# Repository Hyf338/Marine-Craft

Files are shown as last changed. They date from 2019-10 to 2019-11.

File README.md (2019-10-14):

# JMU_ETA_Fly on The Sea

<p align="center">
  
</p>

## 简介
2019集大电协 海洋航行器

工具     | 描述
-------- | -----
Altium Design|PCB设计
Keil|软件编程
123D Design|3D软件

## 目录说明
````
+——Marine craft
|---- Dos: 【设计文档】
|---- 3D model: 【3D模型】
|----+ hardware:【电路设计】  
|       ├──Control V1.0【主控板】
|       ├──Control V2.0【主控电路板-最终版】
|       ├──Infrared reception【红外接收盘】
|       ├──Power Transfer【临时电源转接】
|---+ software:【软件设计】
|       ├──Craft【航行器程序】
|       ├──remoted【遥控器调试】
````

## 3D model
- 红外屏蔽罩3D模型设计

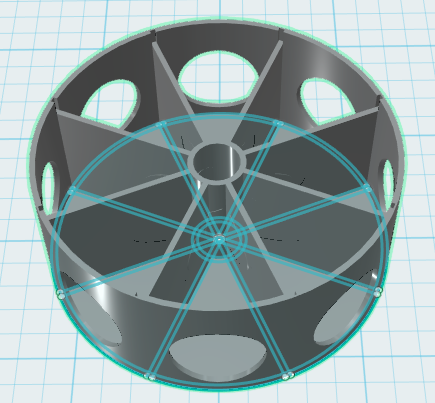
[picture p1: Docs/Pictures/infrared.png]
3D信号屏蔽罩 信号屏蔽罩


## Hardware
- 主控与外设描述

硬件     | 描述
-------- | -----
芯片信号  |STM32F103
串口  | ZIGBEE
蓝牙  | HC-05
舵机  | EMAX ES08MA
电机|380
显示|oled

- 端口定义

功能     | 端口
-------- | -----
红外盘接收  |A8.B13.B14.B15.C6.C7.C8.C9
蓝牙&串口  | USART2_TX -- A2  . USART2_RX -- A3
蓝牙&串口  | USART1_TX -- A9  . USART1_RX -- A10
舵机  | TIM2_CH2 -- A1
电机|TIM3_CH1 --B4 .   TIM3_CH2 -- B5
OLED|DC -- B6. RES -- B7 . D1 -- B8 . D0 -- B9

- [x]  船舶主控板

- 航行器主控板模块流程图

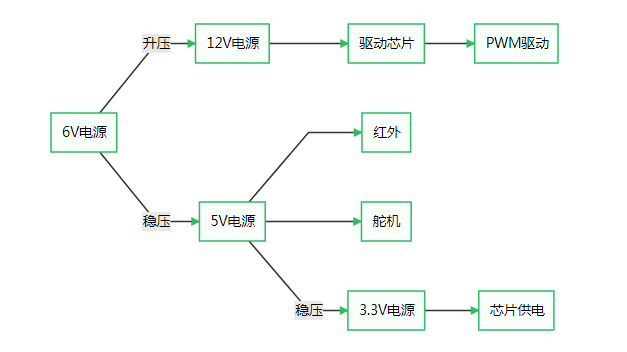
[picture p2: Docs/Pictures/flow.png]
流程图


- 航行器主控板

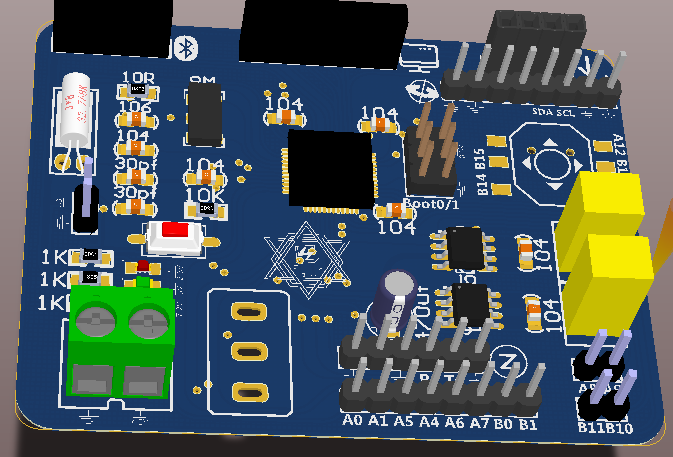
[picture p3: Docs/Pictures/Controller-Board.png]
主控板


- [x] 一体化红外接收盘

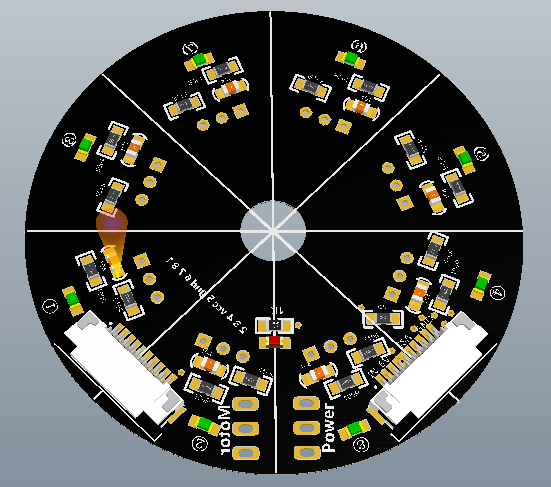
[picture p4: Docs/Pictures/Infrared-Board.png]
一体化红外接收盘


## Software

### 两种模式

- [x] 自动追踪模式
- [x] 遥控模式
- 数据包通信协议

| 编号 | 1 | 2 | 3 | 4 | 5 | 6 | 7 | 
| --- | --- | --- | --- | --- | --- | --- | --- |
| 数据所代表的含义 | 模式位 | 包头 | 包头 | 数据长度位 | 舵机 | 电机 | 校验 | 
| 说明 | 1-遥控、0-追踪 | AA | 55 | 2 | Servo | Motor | 累加 |
| 数组编号 | 0 | 1 | 2 | 3 | 4 | 5 | 6 |

## 作品

### 船模

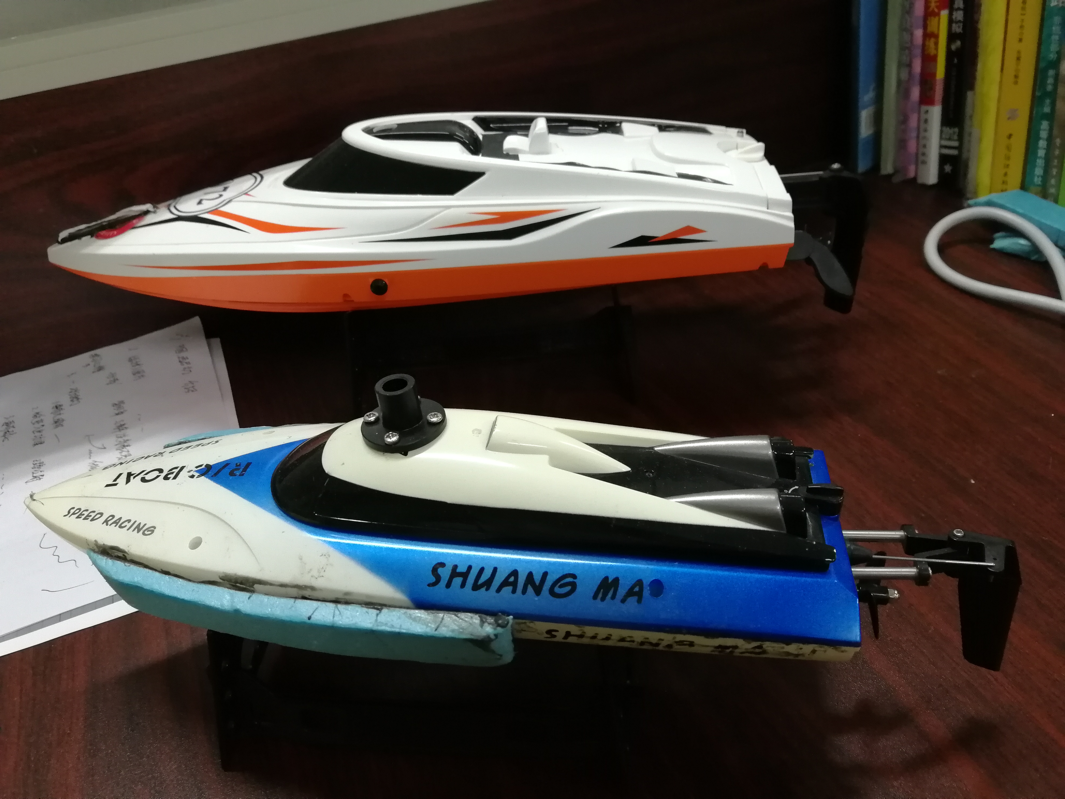
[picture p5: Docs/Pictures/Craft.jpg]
航行器


### 遥控器

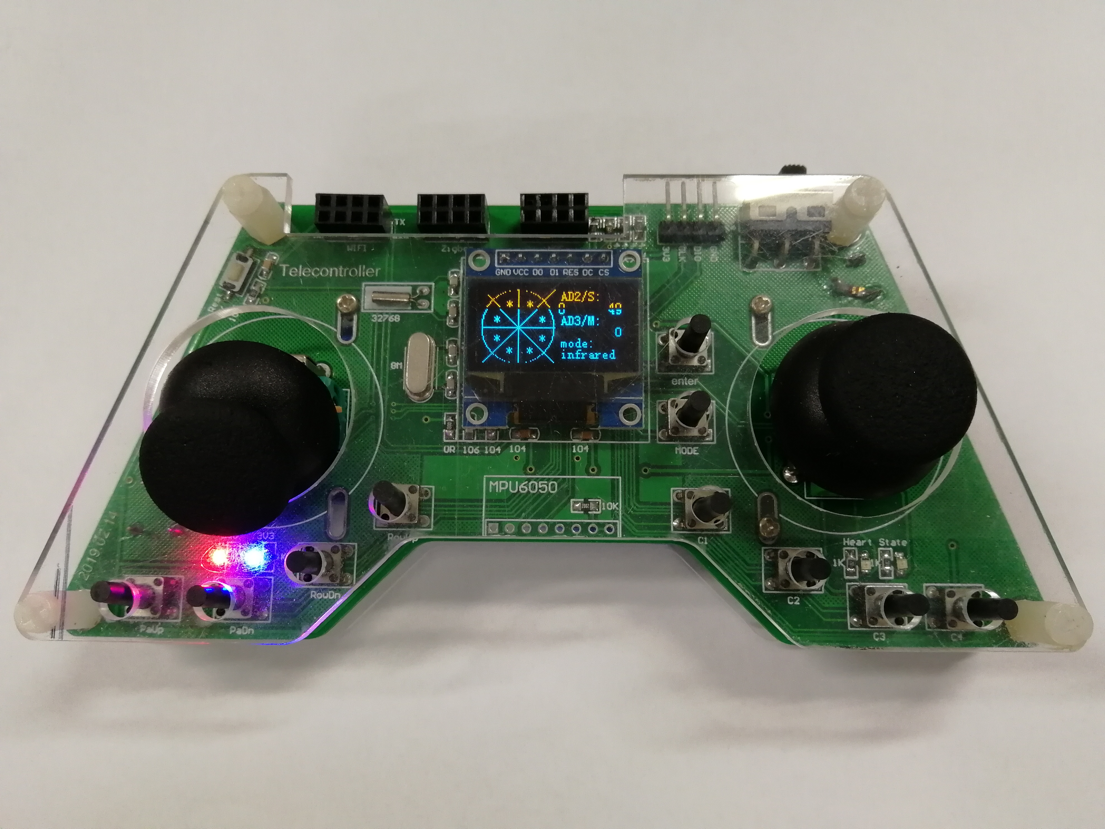
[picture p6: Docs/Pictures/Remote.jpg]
遥控器


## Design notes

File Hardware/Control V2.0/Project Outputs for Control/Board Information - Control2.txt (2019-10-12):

Board Information Report
Filename     : D:\AD\船模主控板\Control\Control2.PcbDoc
Date         : 2019/3/17
Time         : 16:33:21
Time Elapsed : 00:00:00

Routing Information
    Routing completion, 100.00%
    Connections, 214
    Connections routed, 214
    Connections remaining, 0
count : 4

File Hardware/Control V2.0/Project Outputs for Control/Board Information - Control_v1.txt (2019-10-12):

Board Information Report
Filename     : C:\Users\dell\Desktop\JMU_ETA_Fly-on-The-Sea\船模主控板\Control\Control_v1.1.PcbDoc
Date         : 2019/6/20
Time         : 21:29:51
Time Elapsed : 00:00:00

Routing Information
    Routing completion, 100.00%
    Connections, 204
    Connections routed, 204
    Connections remaining, 0
count : 4

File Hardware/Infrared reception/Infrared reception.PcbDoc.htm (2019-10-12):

Reporting Options

# File in Previous Format

Date | : | 2019/10/12
Time | : | 8:33:09
Filename | : | D:\Git Project\Marine Craft\Infrared reception\PCB_Project\Infrared reception.PcbDoc

Version | Warning

This file was generated by an earlier version of the software

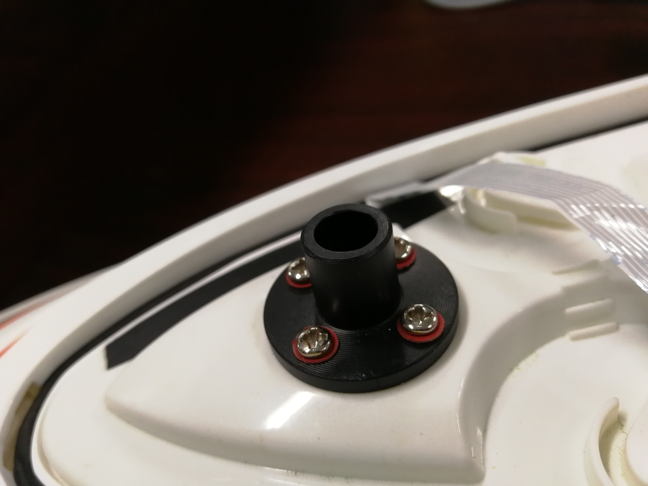
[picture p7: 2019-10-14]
Docs/Pictures/Support.jpg

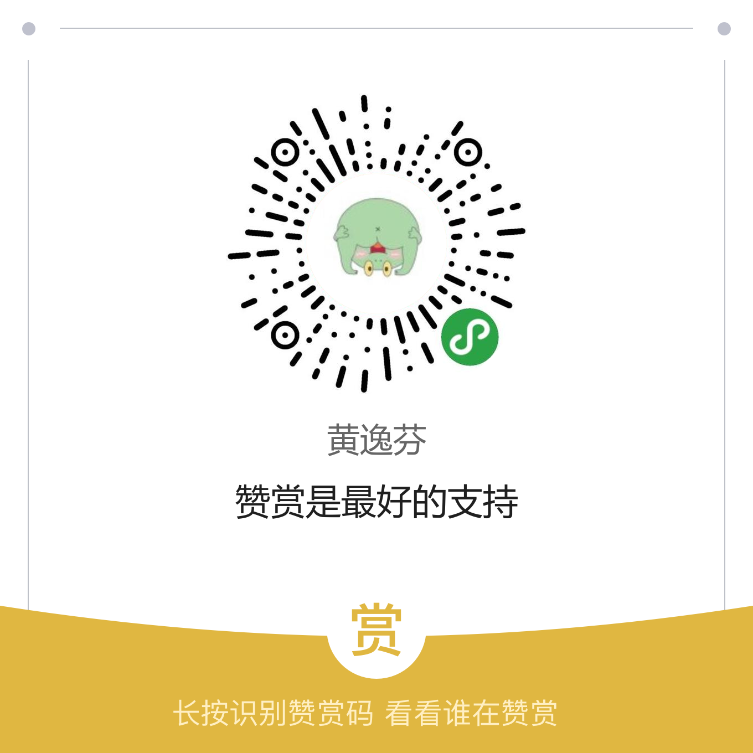
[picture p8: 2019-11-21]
Docs/Pictures/zan.png

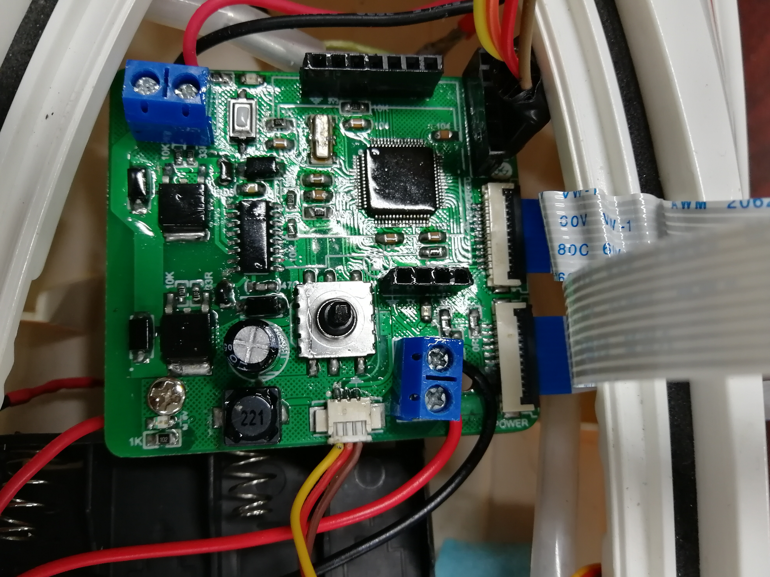
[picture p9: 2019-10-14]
Docs/Pictures/Board.jpg

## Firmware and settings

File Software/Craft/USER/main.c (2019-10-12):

#include "stm32f10x.h"
#include "delay.h"
#include "sys.h"
#include "timer.h"
#include "key.h"
#include "oled.h"
#include "control.h"
#include "usart.h"



int Motor1=150;
int Motor2=0;
u8 key_v=0,mode=0;
u8 receive_motor=0,receive_servo=0;
int servo=1210;
extern int Expect_servo;
extern int servo_PWM;
extern u8 infrared;
extern void infrared_Init(void);
extern u8 infrared_bit_move(void);
extern void infrared_receive(void);
extern void TIM4_Int_Init(u16 arr,u16 psc);
extern void servo_PD(void);
extern void infrared_receive_1(void);
extern void infrared_receive_2(void);


void page()
{
			static u8 x=0,y=0;
	draw_circle(35,30,30);
		for(x = 70;x>=30;x--)
		{
				OLED_DrawPoint(108-0.5*x,x,1);//画斜线 斜率≈√3/3
				OLED_DrawPoint(17 +0.5*x,x,1);
				y = 30-x;
				OLED_DrawPoint(64-0.5*y,y,1);
				OLED_DrawPoint(64+0.5*y,y,1);
			  OLED_Refresh_Gram();//更新显示到OLED
		}

	OLED_Refresh_Gram();
}


 int main(void)
 {	
  KEY_Init(); //IO初始化
	delay_init();	    	 //延时函数初始化	 
	OLED_Init();//OLED初始化
  uart2_init(115200);
//  Boot_Animation();	
	NVIC_PriorityGroupConfig(NVIC_PriorityGroup_2); 	 //设置NVIC中断分组2:2位抢占优先级，2位响应优先级
 	TIM3_PWM_Init(499,71);	 //72分频，500重装载值  f=2k Hz   电机
	TIM2_PWM_Init(20000 ,71); //72分频，20000重装载值   f= 50 Hz； 舵机
	TIM4_Int_Init(50000,35);//144分频，50000重装载值   f= 10Hz，T=100ms；红外接收检测周期为108ms；采集时间
	TIM_ITConfig(TIM4,TIM_IT_Update,DISABLE ); //关闭定时器TIM4中断，
	
	
//	OLED_ShowString(10, 5,(u8 *)"2019.3.17",12);
//	OLED_ShowString(10,15,(u8 *)"Motor1:",12);
//	OLED_ShowString(10,25,(u8 *)"Servo:",12);
//	OLED_ShowString(10,35,(u8 *)"infrared:",12);
//	OLED_ShowString(10,45,(u8 *)"servo_PWM:",12);
//	OLED_Refresh_Gram();
	infrared_Init();
	TIM_SetCompare2(TIM2,1210);	//舵机
	delay_ms(10);
	 
  while(1)
	{
 	
		
		key_v=KEY_Scan(0);
	
		if(key_v==KEY_UP_PRES) Motor1+=10;
		if(key_v==KEY_DOWM_PRES) Motor1-=10;
		
//		OLED_ShowNum(75,15,Motor1,3,12);
//		OLED_ShowNum(85,35,infrared,3,12);
//		OLED_ShowNum(85,45,servo,4,12);
		if(mode==0)
		{
			Motor1=150;
			TIM_ITConfig(TIM4,TIM_IT_Update,ENABLE ); //使能指定的TIM3中断,允许更新中断
//			infrared_receive_1();
			infrared_receive_1();
			TIM_ITConfig(TIM4,TIM_IT_Update,DISABLE ); //关闭定时器TIM4中断，
			servo=Expect_servo;
			if(infrared==0xff)  Motor1=0; 
				else Motor1=150;
		}
		if(mode==1)
		{
			Motor1=2*receive_motor;
			servo=1210+5*(50-receive_servo);
		}
		
	 servo= (servo>1600)? 1600:servo;
	 servo= (servo<850)? 850:servo;
				
		
		TIM_SetCompare2(TIM2,servo);	//舵机
		TIM_SetCompare2(TIM3,Motor2);		   
		TIM_SetCompare1(TIM3,Motor1);	 
		page();
	}	 	
 }

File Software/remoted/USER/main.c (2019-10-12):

#include "stm32f10x.h"

#include "mpuiic.h"
#include "mpu6050.h"
#include "inv_mpu.h"
#include "inv_mpu_dmp_motion_driver.h" 

#include "delay.h"
#include "oled.h"
#include "usart.h"
#include "timer.h"
#include "control.h"
#include "key.h"
#include "adc.h"
#include "display.h"

/****************************************************************
硬件连接:

Zigbee(uart1):			ESP8266(uart2):				NRF24L01:
TX -> PA9						TX -> PA2							NRF_CE -> PA0
RX -> PA10					RX -> PA3							NRF_CS -> PA1
																					NRF_IRQ -> PA4
																					SPI1_CLK -> PA5
																					SPI1_MISO -> PA6
																					SPI1_MOSI -> PA7
												
指示灯:							蜂鸣器:								OLED:
State -> PB12				BUZZ -> PB4						D0 -> PB9
Heart -> PB13															D1 -> PB8
																					RES -> PB7
																					DC -> PB6
																					
按键:								摇杆:										
PaUp -> PC4         Throttle -> PC2					
PaDn -> PC5         Yaw -> PC3							
RowUp -> PB1        Pitch -> PC1
RowDn -> PB0        Roll -> PC0
enter -> PC9
MODE -> PC8
C1 -> PB14
C2 -> PB15
C3 -> PC6
C4 -> PC7


MPU6050:
IMUSCL -> PB10
IMUSDA -> PB11
****************************************************************/

float pitch,roll,yaw; 		//欧拉角									//俯仰角		翻滚角		横向角
short aacx,aacy,aacz;		//加速度传感器原始数据
short gyrox,gyroy,gyroz;	//陀螺仪原始数据
short temp;					//温度
char AD1=0,AD2=0,AD3=0,AD4=0;
short AD1_get=0,AD2_get=0,AD3_get=0,AD4_get=0;

extern signed short int Pitch,Roll,Yaw;
extern u8 send_data;

typedef enum
{
	sunday,  //0
	monday,
	thuesday,
	wednesday = 5,
	tuesday,
	friday,
	saturday
}WeekType;

WeekType week;

 int main(void)
 {
	 
	 delay_init();	    	//延时函数初始化
	 NVIC_PriorityGroupConfig(NVIC_PriorityGroup_2);// 设置中断优先级分组2
	
	
	 OLED_Init();
	 BUZZ_Init();
//	 uart_init(115200);//zigbee串口通信
	 KEY_Init(); //IO初始化
	 Adc_Init();

	 
	 MPU_Init();					//初始化MPU6050
	 
	 while(mpu_dmp_init())
   {
		OLED_ShowString1(0,3,"Error");
		delay_ms(200);
   }
	 
   TIM4_Int_Init(50000,107);
	 TIM_Cmd(TIM4, ENABLE);  //使能TIMx
		OLED_Clear();
   while(1)
	 {		 
		 AD1_get=Get_Adc_Average(ADC_Channel_10,10);
		 AD2_get=Get_Adc_Average(ADC_Channel_11,10);
		 AD3_get=Get_Adc_Average(ADC_Channel_12,10);
		 AD4_get=Get_Adc_Average(ADC_Channel_13,10);
		 
		 AD2=100*AD2_get/4096;
		 AD3=100*(4096-AD3_get)/4096;
		 
		 Page2();
	 }
 }

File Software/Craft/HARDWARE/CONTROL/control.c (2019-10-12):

#include "sys.h"
#include "stm32f10x.h"
#include "control.h"
#include "timer.h"
#include "delay.h"

#define servo_mid 1210
#define N 5

int Expect_servo=0;
int servo_PWM=1210;
int servo_last=0;
int Servo_err=0;
//---------------------------
u8 infrared=0x00;//初始状态
char temp=0x00;
char infrared_flag=0;
u8  infrared_bit[8]={0};
int servo_err[4]={0,0,0,0};
u8 sum=0;
int infrared_err=0;

/*红外引脚初始化函数*/
void infrared_Init(void) //IO初始化
{ 
 	GPIO_InitTypeDef GPIO_InitStructure;
 
 	RCC_APB2PeriphClockCmd(RCC_APB2Periph_GPIOA|RCC_APB2Periph_GPIOB|RCC_APB2Periph_GPIOC,ENABLE);//使能PORTA,PORTE时钟

	GPIO_InitStructure.GPIO_Pin  = GPIO_Pin_6 |GPIO_Pin_7|GPIO_Pin_8|GPIO_Pin_9;//
	GPIO_InitStructure.GPIO_Mode = GPIO_Mode_IPU; //设置成上拉输入
 	GPIO_Init(GPIOC, &GPIO_InitStructure);//初始化GPIOC
	
	GPIO_InitStructure.GPIO_Pin  = GPIO_Pin_8;//
	GPIO_InitStructure.GPIO_Mode = GPIO_Mode_IPU; //设置成上拉输入
 	GPIO_Init(GPIOA, &GPIO_InitStructure);//初始化GPIOA
	
	GPIO_InitStructure.GPIO_Pin  = GPIO_Pin_13|GPIO_Pin_14|GPIO_Pin_15;//
	GPIO_InitStructure.GPIO_Mode = GPIO_Mode_IPU; //设置成上拉输入
 	GPIO_Init(GPIOB, &GPIO_InitStructure);//初始化GPIOA
}


/*红外检测位移函数，
	目标：把八个红外头按位移入一个char型数据，方便写switch和case语句
	数值说明：0为接收到红外信号，1未接收到信号。无信号的状态为0xff
*/
	
u8 infrared_bit_move(void)
{
	
	char i=0;
	infrared=0xff;
	temp=0x00;
	
	while(!infrared_flag)
	{
		infrared_bit[0]=GPIO_ReadInputDataBit(GPIOB,GPIO_Pin_13);//1-8号红外按序排列
		infrared_bit[1]=GPIO_ReadInputDataBit(GPIOA,GPIO_Pin_8);
		infrared_bit[2]=GPIO_ReadInputDataBit(GPIOC,GPIO_Pin_9);
		infrared_bit[3]=GPIO_ReadInputDataBit(GPIOC,GPIO_Pin_8);
		infrared_bit[4]=GPIO_ReadInputDataBit(GPIOC,GPIO_Pin_7);
		infrared_bit[5]=GPIO_ReadInputDataBit(GPIOC,GPIO_Pin_6);
		infrared_bit[6]=GPIO_ReadInputDataBit(GPIOB,GPIO_Pin_15);
		infrared_bit[7]=GPIO_ReadInputDataBit(GPIOB,GPIO_Pin_14); 
	
		for(i=0;i<8;i++)//检测到为0，bit[0] 最低位
		{
			temp = temp<<1;
			temp|=infrared_bit[7-i];
		}
		infrared&=temp;
		
	}
	
	if(infrared_flag==1) infrared_flag=0;
	
	return infrared;
}




/*红外接收处理函数*/
void infrared_receive_1()
{
	infrared=filter();
	switch(infrared)
		
	{
		case 0xfe:Expect_servo=900;break;//1号
		case 0xfd:Expect_servo=900;break;//2
		case 0xfb:Expect_servo=1600;break;//3
		case 0xf7:Expect_servo=1600;break;//4
		case 0xef:Expect_servo=1600;break;//5
		case 0xdf:Expect_servo=1600;break;//6
		case 0xbf:Expect_servo=900;break;//7
		case 0x7f:Expect_servo=1210;break;//8
		
		case 0x7e:Expect_servo=900;break;
		case 0xfc:Expect_servo=900;break;
		case 0xf9:Expect_servo=900;break;
		case 0xf3:Expect_servo=1600;break;
		case 0xe7:Expect_servo=1600;break;
		case 0xcf:Expect_servo=1600;break;
		case 0x9f:Expect_servo=1210;break;
		case 0x3f:Expect_servo=900;break;
		
		case 0x3e:Expect_servo=1200;break;
		case 0x7c:Expect_servo=900;break;
		case 0xf8:Expect_servo=900;break;
		case 0xf1:Expect_servo=1600;break;
		case 0xe3:Expect_servo=1600;break;
		case 0xc7:Expect_servo=1600;break;
		case 0x8f:Expect_servo=900;break;
		case 0x1f:Expect_servo=900;break;
		
		case 0x1e:Expect_servo=900;break;
		case 0x3c:Expect_servo=900;break;
		case 0x78:Expect_servo=900;break;
		case 0xf0:Expect_servo=1600;break;
		case 0xe1:Expect_servo=1600;break;
		case 0xc3:Expect_servo=1600;break;
		case 0x87:Expect_servo=1600;break;
		case 0x0f:Expect_servo=1210;break;
		
		case 0xce:Expect_servo=1600;break;
		case 0x1c:Expect_servo=1600;break;
		case 0x38:Expect_servo=1600;break;
		case 0x70:Expect_servo=1600;break;
		case 0xe0:Expect_servo=900;break;
		case 0xc1:Expect_servo=1200;break;
		case 0x83:Expect_servo=900;break;
		case 0x07:Expect_servo=900;break;
		
		case 0x06:Expect_servo=1210;break;
		case 0x0c:Expect_servo=900;break;
		case 0x18:Expect_servo=900;break;
		case 0x30:Expect_servo=900;break;
		case 0x60:Expect_servo=1600;break;
		case 0xc0:Expect_servo=1600;break;
		case 0x81:Expect_servo=1600;break;
		case 0x03:Expect_servo=1600;break;
		
		case 0x02:Expect_servo=1600;break;
		case 0x04:Expect_servo=900;break;
		case 0x08:Expect_servo=1200;break;
		case 0x10:Expect_servo=900;break;
		case 0x20:Expect_servo=900;break;
		case 0x40:Expect_servo=1600;break;
		case 0x80:Expect_servo=1600;break;
		case 0x01:Expect_servo=1600;break;

		
		default:Expect_servo=Expect_servo;break;
	}
	
	 Expect_servo= (Expect_servo>1600)? 1600:Expect_servo;
	 Expect_servo= (Expect_servo<850)? 850:Expect_servo;

}

//方法2：不使用case语句，
void infrared_receive_2()
{
	u8 i=0;
	sum=0;
	infrared=filter();
	infrared_err+=(infrared|0x7f)==0x7f? 400:0;//300:0;	//8号
	infrared_err+=(infrared|0xbf)==0xbf? 400:0;//150:0; //7号
	infrared_err+=(infrared|0xdf)==0xdf? -300:0;//-150:0;		//6号
	infrared_err+=(infrared|0xef)==0xef? -300:0;//-300:0;//5号
	infrared_err+=(infrared|0xfe)==0xfe? -300:0;//-300:0;//4号
	infrared_err+=(infrared|0xfd)==0xfd? -300:0;//-300:0;//3号
	infrared_err+=(infrared|0xfb)==0xfb? 400:0;//300:0;
	infrared_err+=(infrared|0xf7)==0xf7? 400:0;//300:0;
	
	for(i=0;i<8;i++)
	{
		sum+=(infrared>>i)&1;//算1的个数
	}
	sum=8-sum;//算0的个数
	if(sum!=0)//有接收
	{
		Expect_servo=(int)(servo_mid-infrared_err/sum);
	}
	
	 Expect_servo= (Expect_servo>1600)? 1600:Expect_servo;
	 Expect_servo= (Expect_servo<850)? 850:Expect_servo;
}

char filter(void)
{

   char value_buf[N];
   char count,i,j,temp;
   for ( count=0;count<N;count++)
   {
      value_buf[count] = infrared_bit_move();
   }
   for (j=0;j<N-1;j++)
   {
      for (i=0;i<N-j;i++)
      {
         if ( value_buf[i]>value_buf[i+1] )
         {
            temp = value_buf[i];
            value_buf[i] = value_buf[i+1]; 
             value_buf[i+1] = temp;
         }
      }
   }
   return value_buf[(N-1)/2];
}


void servo_PD()
{
	 u8 i=0;
//	 static int expect_s[3]={0,       0,0};
	 u8 servo_p=1;//10为满值
	 u8 servo_d=1;//10为满值
	 
	 servo_err[3]=(int)(servo_p*(Expect_servo-servo_mid)+servo_d*(servo_err[3]-servo_last));
	 servo_last=servo_err[3];
	 
	 for(i=0;i<2;i++)
	 servo_err[i]=servo_err[i+1];//滑动滤波
   Servo_err=0.85*servo_err[3]+0.08*servo_err[2]+0.05*servo_err[1]+0.02*servo_err[0];
	 servo_PWM=servo_mid-Servo_err;
	 servo_PWM= (servo_PWM>1600)? 1600:servo_PWM;
	 servo_PWM= (servo_PWM<850)? 850:servo_PWM;
}

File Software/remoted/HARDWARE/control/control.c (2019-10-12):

#include "control.h"
#include "sys.h"

#include "mpuiic.h"
#include "mpu6050.h"
#include "inv_mpu.h"
#include "inv_mpu_dmp_motion_driver.h" 
#include "usart.h"
#include "oled.h"

/*
	pitch    short     						原始数据
	Pitch    signed short int     强制转化成有符号16位
	pitch_L  short int        		低八位
*/

u8 send_data[8]={0,0,0,0,0,0,0,0};
signed short int test_1=0;
int test_size=0;
signed short int pitch_L=0,pitch_H=0,roll_L=0,roll_H=0,yaw_L=0,yaw_H=0;
signed short int Pitch=0,Roll=0,Yaw=0;


extern float pitch,roll,yaw; 		//欧拉角									//俯仰角		翻滚角		横向角
extern short aacx,aacy,aacz;		//加速度传感器原始数据
extern short gyrox,gyroy,gyroz;	//陀螺仪原始数据
extern short temp;					//温度
extern short AD1,AD2,AD3,AD4;

void BUZZ_Init(void)
{
	GPIO_InitTypeDef  GPIO_InitStructure;
 	RCC_APB2PeriphClockCmd(RCC_APB2Periph_GPIOB, ENABLE);	 //使能PA,PD端口时钟
	RCC_APB2PeriphClockCmd(RCC_APB2Periph_AFIO,ENABLE);
	GPIO_PinRemapConfig(GPIO_Remap_SWJ_JTAGDisable, ENABLE);
	
	GPIO_InitStructure.GPIO_Pin = GPIO_Pin_4;				 //LED0-->PA.8 端口配置
	GPIO_InitStructure.GPIO_Mode = GPIO_Mode_Out_PP; 		 //推挽输出
	GPIO_InitStructure.GPIO_Speed = GPIO_Speed_50MHz;		 //IO口速度为50MHz
	GPIO_Init(GPIOB, &GPIO_InitStructure);					 //根据设定参数初始化GPIOA.8
	GPIO_ResetBits(GPIOB,GPIO_Pin_4);						 //PA.8 输出高
}
 


void angle_get()
{
	if(mpu_dmp_get_data(&pitch,&roll,&yaw)==0)
	{ 
		temp=MPU_Get_Temperature();	//得到温度值
		MPU_Get_Accelerometer(&aacx,&aacy,&aacz);	//得到加速度传感器数据
		MPU_Get_Gyroscope(&gyrox,&gyroy,&gyroz);	//得到陀螺仪数据
	}
}



void data_process()
{
	u8 i=0;
	
	Pitch=(signed short int)pitch;
	Roll=(signed short int)roll;
	Yaw=(signed short int)yaw;
	
	send_data[i++]=0xaa;
	
	pitch_L=Pitch&0x00ff;
	send_data[i++]=pitch_L;
	pitch_H=Pitch&0xff00;
	pitch_H>>=8;
	send_data[i++]=pitch_H;
	
	roll_L=Roll&0x00ff;
	send_data[i++]=roll_L;
	roll_H=Roll&0xff00;
	roll_H>>=8;
	send_data[i++]=roll_H;
	
	yaw_L=Yaw&0x00ff;
	send_data[i++]=yaw_L;
	yaw_H=Yaw&0xff00;
	yaw_H>>=8;
	send_data[i++]=yaw_H;	
	
	if(GPIO_ReadInputDataBit(GPIOC,GPIO_Pin_7)==0)
		send_data[7]=0X01;

}



void datasend()
{
	u8 i=0;
	send_data[i++]=0xaa;
	send_data[i++]=0x55;
	send_data[i++]=AD3;//Motor
	send_data[i++]=AD2;//serve	
	if(GPIO_ReadInputDataBit(GPIOC,GPIO_Pin_4)==0)
		send_data[i++]=0X01;
	if(GPIO_ReadInputDataBit(GPIOC,GPIO_Pin_5)==0)
	send_data[4]=0X00;
}

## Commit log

2019-10-12 【提交】
    [Control.PrjPcb, Control.SchDoc, Control_v1.1.~(20).PcbDoc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]
2019-10-12 【更新】完善说明文档
2019-10-12 【更新】
2019-10-12 【更新】完善文档
2019-10-14 【更新】提交实物图
2019-11-21 【更新】给赞
2019-11-21 【更新】红外盘修改
